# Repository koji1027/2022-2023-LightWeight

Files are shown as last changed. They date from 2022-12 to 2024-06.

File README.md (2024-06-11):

# 高崎高校物理部2年 2022-2023 LightWeight
高崎高校物理部2年チームのGithubリポジトリです。このリポジトリ上の全てのデータは，MIT-Lisenceに従ったうえでの仕様をすべて認めます．

各種リンク
* [ツイッター](https://twitter.com/takataka_robo)
* [ブログ](https://robocup-zunda.hatenablog.com)

## ロボットの機体の概要
ロボットの3Dデータです。-> https://a360.co/3iR0CL1  
3Dデータのリンクが切れている場合は，Hardware/robot.f3z をダウンロードしてFusion360からご覧ください．

以下に、今年度のロボットの基本的なスペックについて示します。
* Main  
  * Raspberry Pi PICO 1個
  * MPU-6050 1個
  * SSD1306 OLEDディスプレイ 1個

* IR Unit
  * TSSP58038 16個
  * TI CD74HC4067 SOIC 1個
  * XIAO SAMD21 1個

* Actuator
  * Maxon RE16 4個
  * Maxon GP16 1:19 4個
  * Pololu G2 18v17 4個
  * 自作オムニホイール 4個
  * XIAO RP2040 1個

* Line Unit
  * NJL7502L 32個
  * WS2812B 32個
  * TI CD74HC4067 SOIC 2個

* Cam
  * OpenMV H7 R2 もしくは UnitV 1個
  
## コーディング規則
簡単なコーディング規則を定めておきます。  
### ファイル構成
プログラムの中核部分を `main.cpp`に書くようにしてください。初見でプログラムを見た際にこのプログラムで大方何をやっているかわかるようにすることを意識してください。`setup()`と`loop()`は他のファイルへ移すことは禁止します。特定の機能にたくさんの記述が必要な場合にはライブラリにしてインクルードしてください。その際、インクルードガードをなるべくつけるようにしましょう。

### 変数・関数・クラス
それぞれの名前は、追加情報なしでもおおよそ役割が推測できる名前にしてくだいさい。例えば、`flag`などといいう名前では、なんのフラグなのかわからないので、`line_flag`などわかりやすい配慮をしてください。定数は、原則大文字で命名してください。  
各ユニットごとに、クラスを作成するようにして下さい。特定のユニットに依存した変数や関数はグローバルで作成するのではなく、各クラスのメンバ変数・関数にしましょう。メンバ変数・関数はできる限り`private`に閉じ込めることが望ましいです。

##コンタクト
もし、なにかありましたらチームリーダへ連絡していただけると幸いです。  
Mail📧&emsp;nkoji.personal@gmail.com&emsp;&emsp;[Twitter](https://twitter.com/negi_robo)

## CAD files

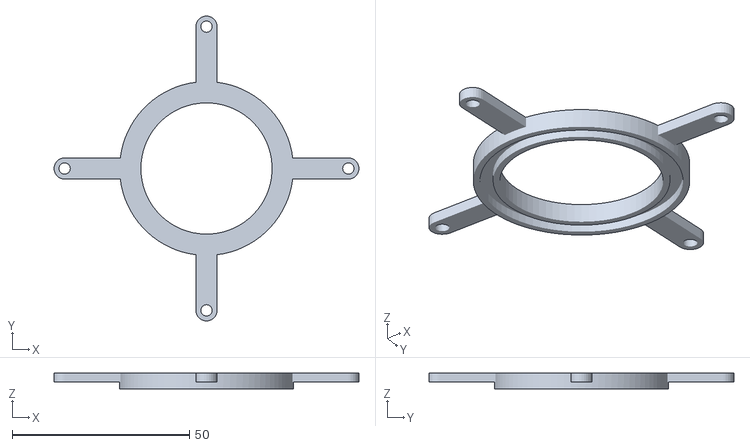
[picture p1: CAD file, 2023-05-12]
Hardware/STL/Pipe Mount GK.stl
86.0 x 86.0 x 4.50

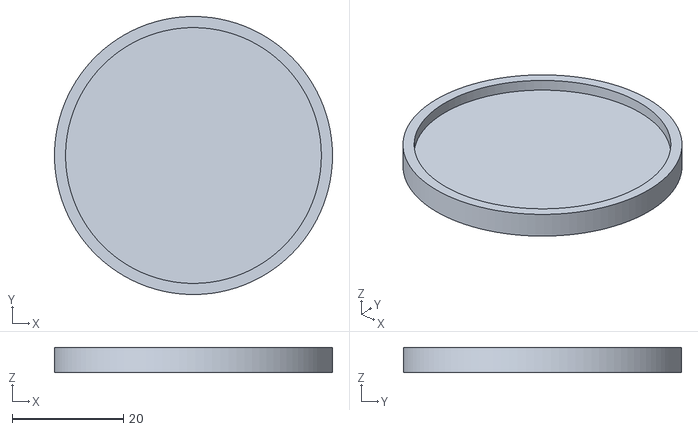
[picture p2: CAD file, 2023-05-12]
Hardware/STL/Top Marker GK.stl
50.0 x 50.0 x 4.50

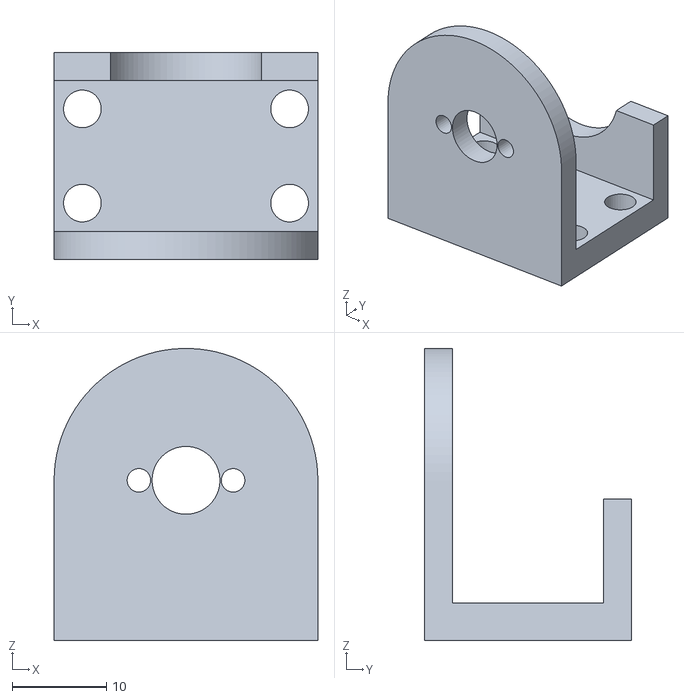
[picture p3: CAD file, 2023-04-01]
Hardware/STL/Motor Mount.stl
28.0 x 22.0 x 31.0

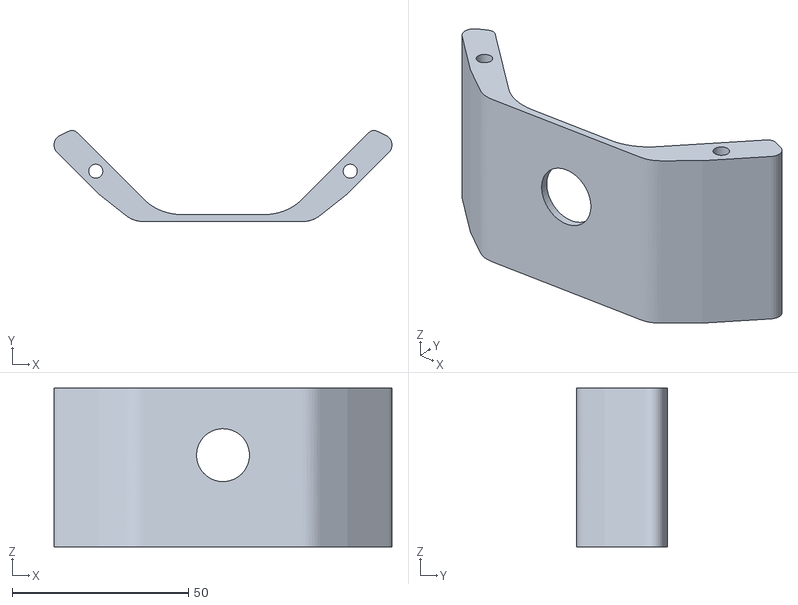
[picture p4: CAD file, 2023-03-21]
Hardware/STL/Front.stl
95.8 x 25.8 x 45.0

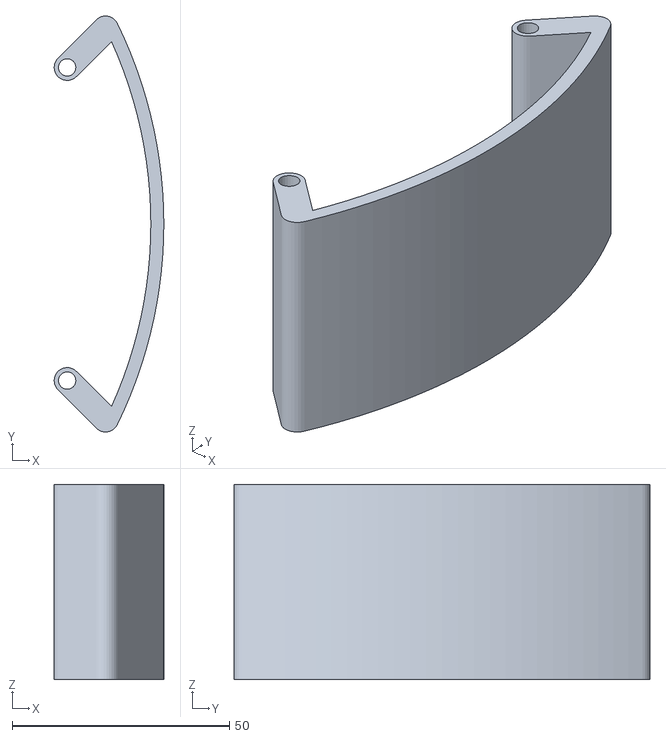
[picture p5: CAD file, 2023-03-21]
Hardware/STL/Right Cover.stl
25.3 x 95.8 x 45.0

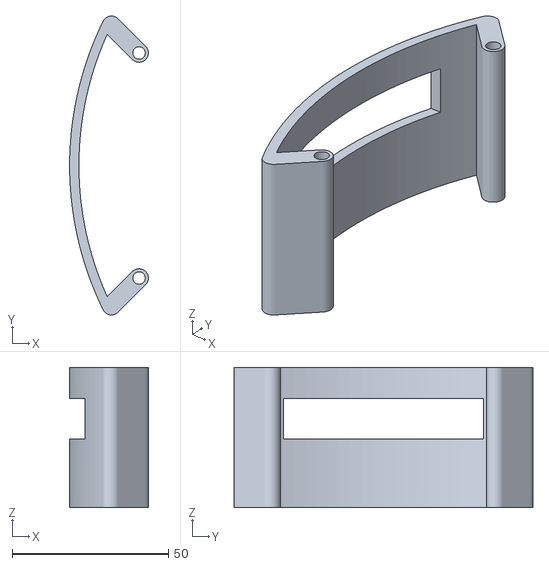
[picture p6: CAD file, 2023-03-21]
Hardware/STL/Left Cover.stl
25.3 x 95.8 x 45.0

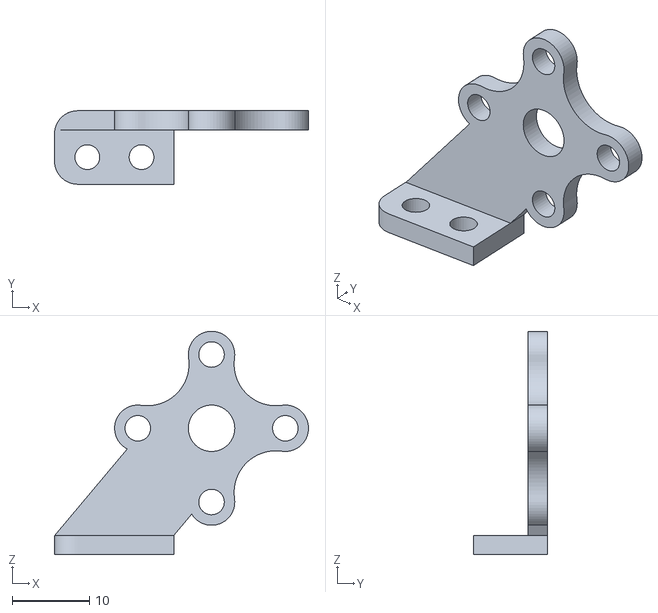
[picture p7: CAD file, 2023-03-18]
Hardware/STL/dribbler.stl
32.8 x 9.50 x 28.8

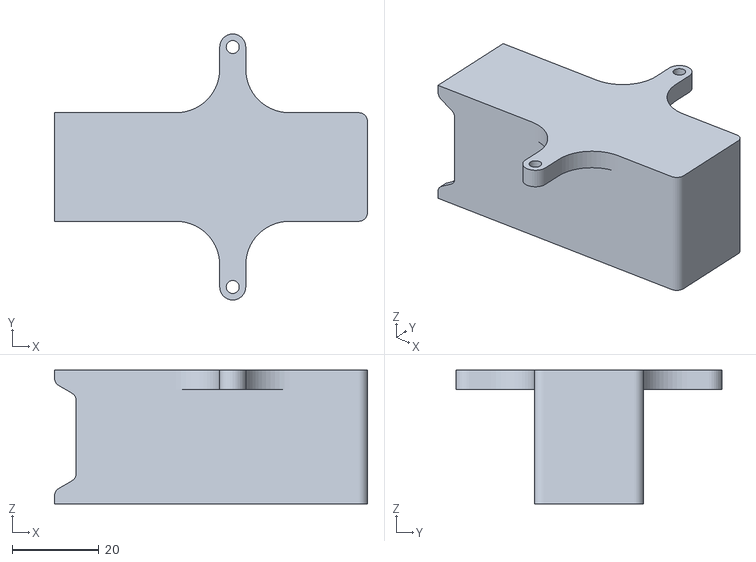
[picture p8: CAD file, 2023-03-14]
Hardware/STL/Battery Case.stl
72.0 x 61.2 x 30.8

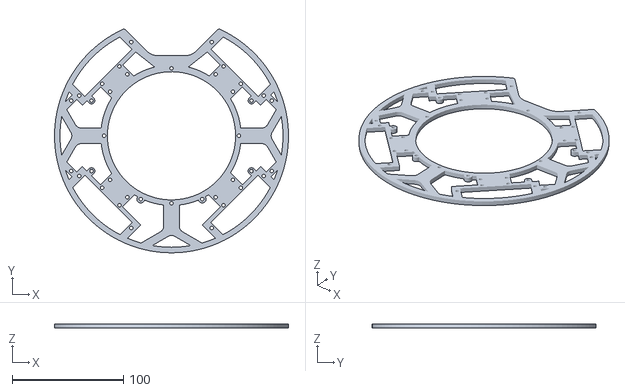
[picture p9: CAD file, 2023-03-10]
Hardware/STL/Bottom.stl
210.0 x 200.7 x 4.00

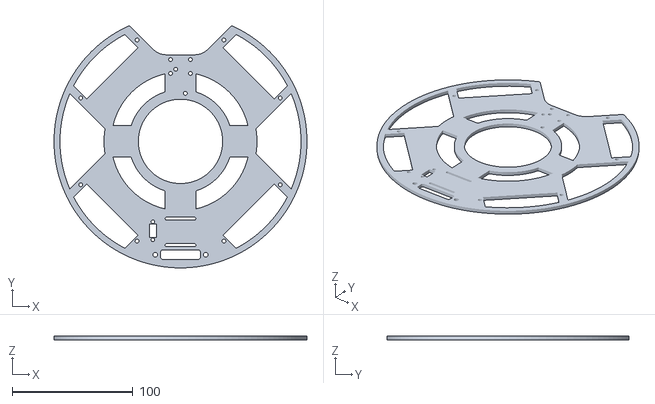
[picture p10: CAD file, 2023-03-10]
Hardware/STL/Top.stl
210.0 x 200.7 x 3.00

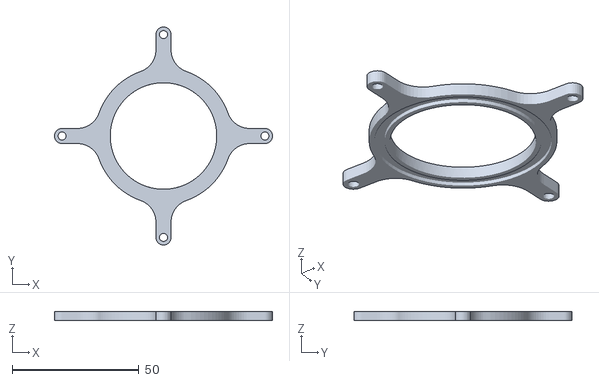
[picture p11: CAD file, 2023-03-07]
Hardware/STL/Pipe Mount FW.stl
86.0 x 86.0 x 3.50

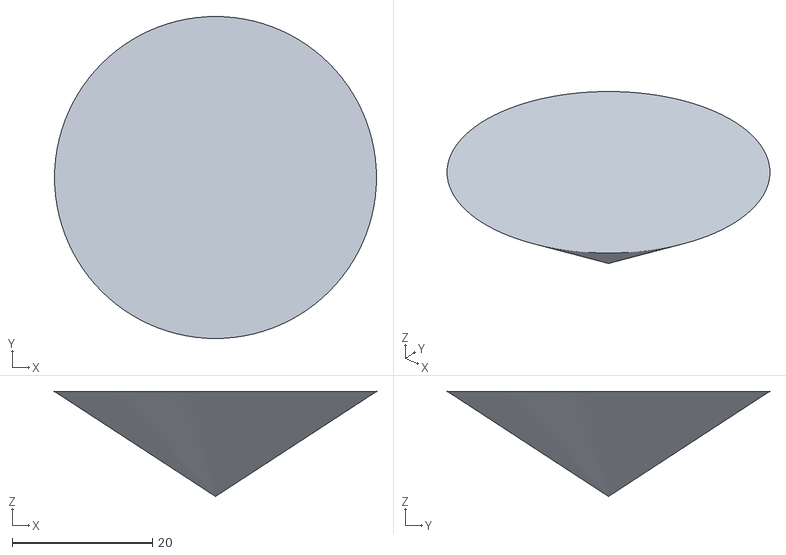
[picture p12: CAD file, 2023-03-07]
Hardware/STL/Mirror 円錐.stl
46.0 x 46.0 x 15.0

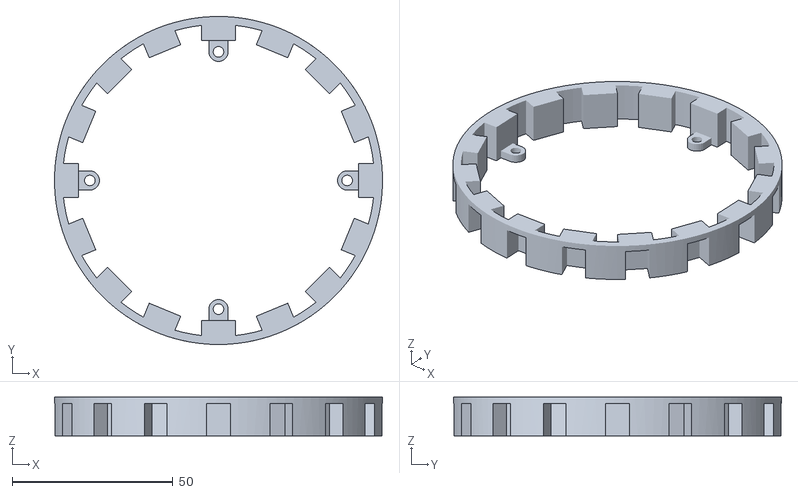
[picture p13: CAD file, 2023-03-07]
Hardware/STL/IR Cover.stl
102.0 x 102.0 x 12.0

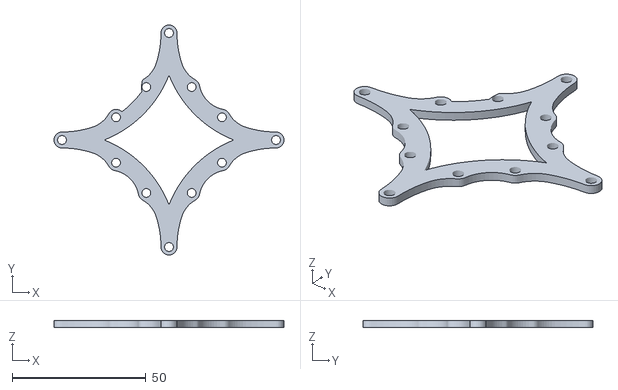
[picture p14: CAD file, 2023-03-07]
Hardware/STL/UnitV mount.stl
86.0 x 86.0 x 2.50

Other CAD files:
Hardware/STL/Back Cover.stl
Hardware/STL/Top Marker FW.stl
Hardware/STL/Test Omni Top.stl
Hardware/STL/OpenMV Mount.stl
Hardware/PCB/Controller.f3z
Hardware/PCB/MotorDriverMount(DRV8874).f3z
Hardware/PCB/MotorDriverMount(Pololu G2).f3z
Hardware/PCB/PowerSupplyBoard.f3z
Hardware/STL/Camera.stl
Hardware/STL/Handle.stl
Hardware/STL/Omini_Bottom.stl
Hardware/STL/Omini_Top.stl
Hardware/STL/OmniWheel_Rev2_1.stl
Hardware/STL/OmniWheel_Rev2_2.stl
Hardware/STL/Test Omni Bottom.stl

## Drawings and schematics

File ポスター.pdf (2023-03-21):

# 高崎高校物理部 二年 Member

## スムーズなチーム連携

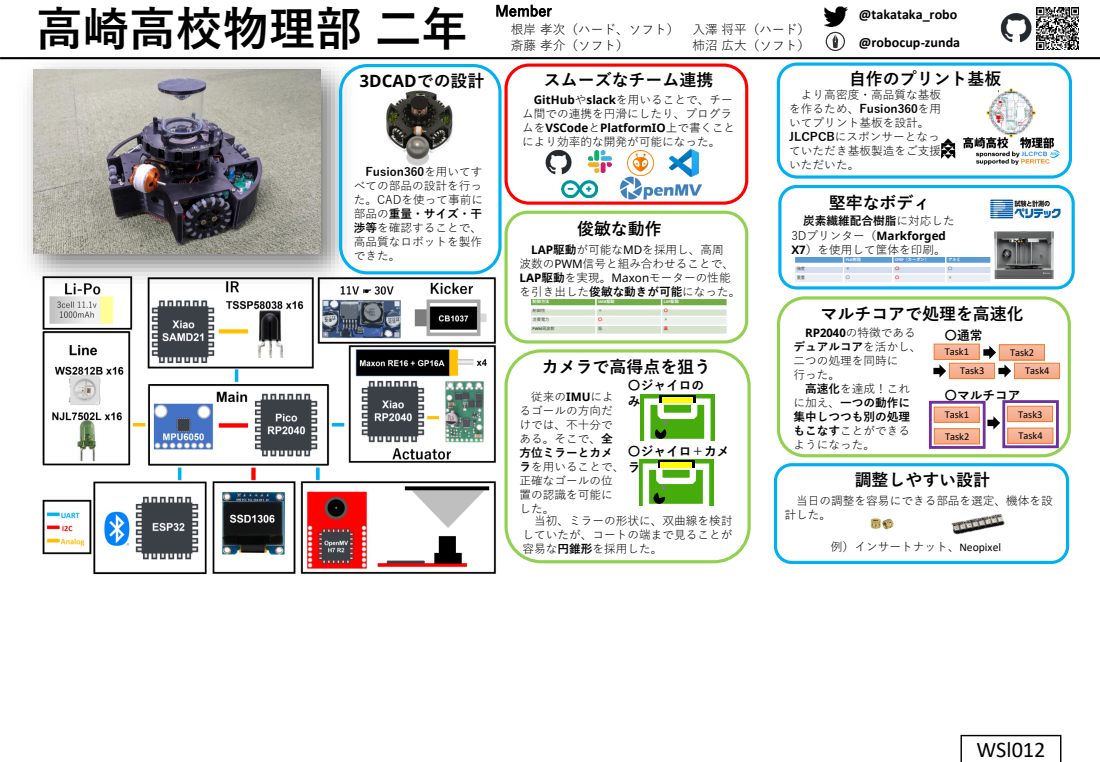
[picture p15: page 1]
斎藤 孝介（ソフト）; 柿沼 広大（ソフト）; @takataka_robo; @robocup-zunda; LAP駆動が可能なMDを採用し、高周 波数のPWM信号と組み合わせることで、 LAP駆動を実現。Maxonモーターの性能 を引き出した俊敏な動きが可能になった。; 俊敏な動作; GitHubやslackを用いることで、チー ム間での連携を円滑にしたり、プログラ ムをVSCodeとPlatformIO上で書くこと により効率的な開発が可能になった。; 堅牢なボディ; 炭素繊維配合樹脂に対応した 3Dプリンター（Markforged X7）を使用して筐体を印刷。; カメラで高得点を狙う; 従来のIMUによ るゴールの方向だ けでは、不十分で ある。そこで、全 方位ミラーとカメ ラを用いることで、 正確なゴールの位 置の認識を可能に した。 当初、ミラーの形状に、双曲線を検討 していたが、コートの端まで見ることが 容易な円錐形を採用した。; 〇ジャイロの み; 〇ジャイロ＋カメ ラ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

根岸 孝次（ハード、ソフト） 入澤 将平（ハード）

PLA樹脂 | CFRP（カーボン） | アルミ

制御方法 | SMB駆動 | LAP駆動

制御性 | × | 〇

消費電力 | 〇 | ×

PWM周波数 | 低 | 高

# 高崎高校物理部 二年 Member

## 堅牢なボディ

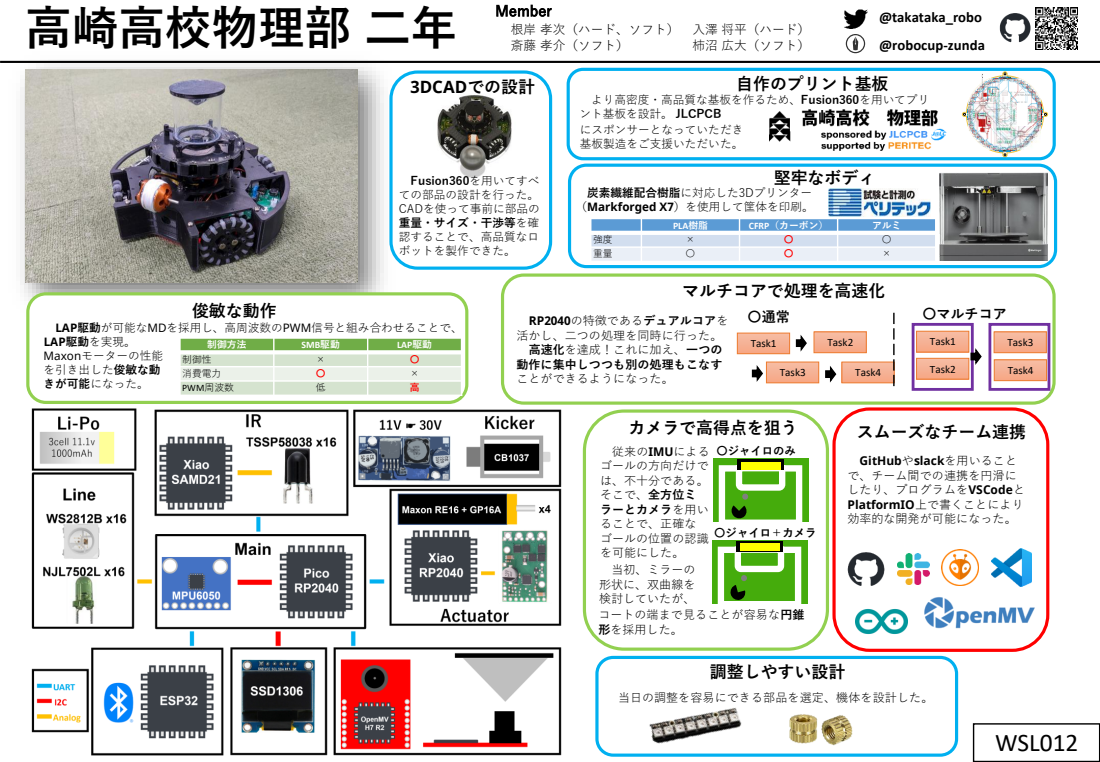
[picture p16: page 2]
斎藤 孝介（ソフト）; 柿沼 広大（ソフト）; @takataka_robo; @robocup-zunda; LAP駆動が可能なMDを採用し、高周波数のPWM信号と組み合わせることで、 LAP駆動を実現。; 俊敏な動作; スムーズなチーム連携; GitHubやslackを用いること で、チーム間での連携を円滑に したり、プログラムをVSCodeと PlatformIO上で書くことにより 効率的な開発が可能になった。; 炭素繊維配合樹脂に対応した3Dプリンター （Markforged X7）を使用して筐体を印刷。; カメラで高得点を狙う; 従来のIMUによる ゴールの方向だけで は、不十分である。 そこで、全方位ミ ラーとカメラを用い ることで、正確な ゴールの位置の認識 を可能にした。 当初、ミラーの 形状に、双曲線を 検討していたが、; 〇ジャイロのみ; 〇ジャイロ＋カメラ; マルチコアで処理を高速化; RP2040の特徴であるデュアルコアを 活かし、二つの処理を同時に行った。 高速化を達成！これに加え、一つの 動作に集中しつつも別の処理もこなす ことができるようになった。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

根岸 孝次（ハード、ソフト） 入澤 将平（ハード）

PLA樹脂 | CFRP（カーボン） | アルミ

強度 | × | 〇 | 〇
重量 | 〇 | 〇 | ×

制御方法 | SMB駆動 | LAP駆動
制御性 | × | 〇
消費電力 | 〇 | ×
PWM周波数 | 低 | 高

# Xiao

# TSSP580

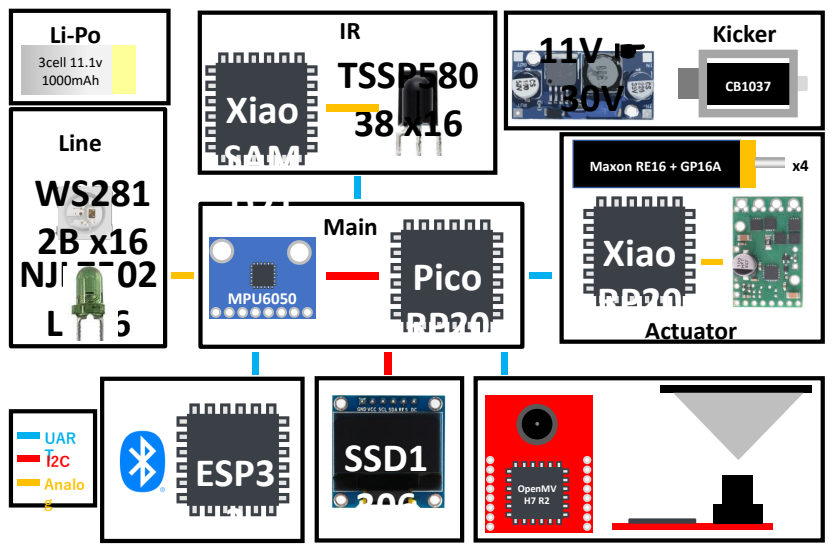
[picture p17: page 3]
Pico RP20 40; MPU6050; Main; NJL7502 L x16; Line; SAM D21; Actuator; 3cell 11.1v 1000mAh; Kicker; Xiao RP20 40; Maxon RE16 + GP16A; ESP3 2; OpenMV H7 R2; SSD1 306; UAR TI2C; Analo g

# Smooth

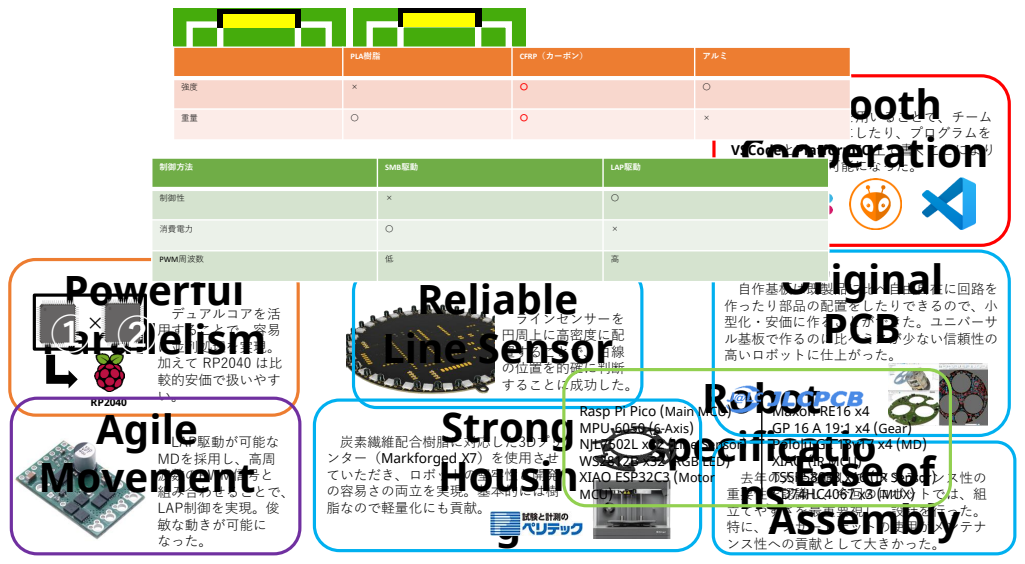
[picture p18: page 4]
Robot specificatio ns; Powerful Parallelism; デュアルコアを活 用することで、容易 に並列処理を実現。 加えて RP2040 は比 較的安価で扱いやす い。; Reliable Line Sensor; ラインセンサーを 円周上に高密度に配 置することで、白線 の位置を的確に判断 することに成功した。; LAP駆動が可能な MDを採用し、高周 波数のPWM信号と 組み合わせることで、 LAP制御を実現。俊 敏な動きが可能に なった。; Agile Movement; Strong Housin g; Cooperation; GitHubやslackを用いることで、チーム 間での連携を円滑にしたり、プログラムを VSCodeとPlatformIO上で書くことにより 効率的な開発が可能になった。; Ease of Assembly; 去年の大会を通して、メンテナンス性の 重要性を認識し、今回のロボットでは、組 立てやすさを最重要視し、設計を行った。 特に、インサートナットの使用がメンテナ ンス性への貢献として大きかった。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

PLA樹脂 | CFRP（カーボン） | アルミ

制御方法 | SMB駆動 | LAP駆動

制御性 | × | 〇

消費電力 | 〇 | ×

PWM周波数 | 低 | 高

Rasp Pi Pico (Main MCU)
MPU-6050 (6-Axis)
NJL7502L x32 (Line Sensor)
WS2812B x32 (RGB LED)
XIAO ESP32C3 (Motor
MCU)

炭素繊維配合樹脂に対応した3Dプリ
ンター（Markforged X7）を使用させ
ていただき、ロボットの堅牢性と開発
の容易さの両立を実現。基本的には樹
脂なので軽量化にも貢献。

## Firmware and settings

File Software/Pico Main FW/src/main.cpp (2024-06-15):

// Arduinoライブラリのインクルード
#include <Arduino.h>

// ライブラリのインクルード
#include <Adafruit_NeoPixel.h>
#include <Adafruit_SSD1306.h>
#include <Servo.h>
#include <stdlib.h>

// 自作ライブラリのインクルード
#include "MPU6050/gyro.h"
#include "line.h"

// 定数の宣言
#define SERIAL_BAUD 115200  // デバッグ用のシリアル通信のボーレート
#define MOTOR_BAUD 115200   // モーターの制御マイコンとの通信のボーレート
#define IR_BAUD 115200      // 赤外線センサー制御マイコンとの通信のボーレート
#define ESP32_BAUD 115200   // ESP32(Bluetooth通信)との通信のボーレート
#define OPENMV_BAUD 115200  // OpenMVとの通信のボーレート
#define OpenMV Serial1      // OpenMVとの通信のシリアルポート
// よく使う角度を定数に保存しておく
#define PI_THIRDS PI / 3.0
#define TWO_THIRDS_PI PI * 2.0 / 3.0
#define PI_EIGHTHS PI / 8.0
#define THREE_EIGHTHS_PI PI * 3.0 / 8.0
#define FIVE_EIGHTHS_PI PI * 5.0 / 8.0
// 回り込みのための計算式の係数
#define CIRC_BASE pow(0.6, 1.0 / 20.0)
#define CIRC_WEIGHT 3.5
// 機体の速度
#define CIRC_SPEED 160
#define STRAIGHT_SPEED 150
#define ESC_LINE_SPEED 190
// ゴールの角度について
#define GOAL_WEIGHT 1.4  // OpenMVからのゴールの角度を使用する際の重み
#define MAX_SIGNAL 2200  // OpenMVからの信号の最大値
#define MIN_SIGNAL 1000  // OpenMVからの信号の最小値
// ピン番号の定義
#define ESC_PIN D14  // ESC(ブラシレスモータードライバー)の制御ピン番号
#define LED_PIN D15  // LEDのピン番号
#define LED_NUM 32   // ラインセンサのLEDの数
// 操作モニターの設定
#define SCREEN_WIDTH 128     // 画面の幅
#define SCREEN_HEIGHT 64     // 画面の高さ
#define SCREEN_ADDRESS 0x3C  // SD1306のアドレス

const uint8_t button_pin[3] = {D18, D19, D20};  // 操作ボタンのピン番号

// インスタンスの生成
Gyro gyro;
Line line;
// Raspberry Pi pico では，PIOという内臓のコンピュータを利用することで，ハードウェアシリアルに似たソフトウェアシリアルを実装されている．
// ハードウェアシリアルが足りのないので，ソフトウェアシリアルを利用する．
SerialPIO motor(D17, D16, 32);  // SerialPIO name(TX, RX, buffer size) の形で宣言する．
SerialPIO ir(D0, D1, 32);
// SerialPIO esp32(D22, D21, 32); //これを使うとプログラムがバグる（詳細は忘れた）．多分，SerialPIOを使いすぎている．
Servo esc;
Adafruit_SSD1306 display(SCREEN_WIDTH, SCREEN_HEIGHT, &Wire, -1);  // モニター

// 全体の制御に関する変数
bool game_flag = false;            // ゲーム中かどうかのフラグ　0:ゲーム中でない, 1:ゲーム中
bool line_set_threshold_flag = 0;  // ラインセンサーの閾値設定フラグ（何に使っていたか忘れた）
double battery_voltage = 0;        // バッテリーの電圧(使ってない)
bool battery_flag = 0;             // バッテリーの電圧が低電圧かどうかのフラグ(使ってない)

// モーターの制御系
// ロボットから見た相対的な角度
double move_angle = 0;     // 進行方向（-PI ~ PI）
double goal_angle = 0;     // ゴールの角度（-PI ~ PI）
uint16_t goal_size = 0;    // ゴールのサイズ(なんで実装したか忘れた)
double machine_angle = 0;  // ロボットに向かせる角度（-PI ~ PI）

// コート全体を俯瞰した時の絶対的な角度
// ゲーム開始時の正面（敵ゴール）方向を０°とし、右回転が正、左回転が負とする。
double abs_move_angle = 0;  // 進行方向（-PI ~ PI）（絶対角度）
double abs_goal_angle = 0;  // ゴールの角度（-PI ~ PI）（絶対角度）
double abs_line_angle = 0;  // ラインの角度（-PI ~ PI）（絶対角度）

bool goal_flag = 0;           // 0:ゴールなし, 1:ゴールあり
uint8_t goal_flag_ratio = 0;  // 忘れた(斎藤に聞けばわかるかも)
uint8_t goal_flag_count = 0;  // 忘れた(斎藤に聞けばわかるかも)
uint8_t speed = 0;            // 速度（0~254）
uint8_t motor_flag = 0;       // モーターの状態についてのフラグ 0: normal, 1: release, 2 or others: brake（0~254）

unsigned long long display_refresh_time = 0;  // ディスプレイのリフレッシュ時間

// fpsを算出するための変数
unsigned long long start_time = 0;
unsigned long long end_time = 0;
int fps = 0;

// 赤外線センサー制御系
double ir_angle = 0;      // 赤外線センサーの角度（-PI ~ PI）
double abs_ir_angle = 0;  // 赤外線センサーの角度（-PI ~ PI）（絶対角度）
uint8_t ir_dist = 0;      // 赤外線センサーの距離（0~254[cm]）(使い物にならなかった)
uint8_t ir_flag = 0;      // ボールが検知されたかどうかのフラグ 0: 有り, 1: なし (0~254)

// 関数の宣言 (setup, loop以外は宣言はここで行い、定義は後で行う)
void motor_uart_send(void);                    // モーター制御系の送信関数
void ir_uart_recv(void);                       // 赤外線センサー制御系の受信関数
void openmv_uart_recv(void);                   // OpenMVとの通信の受信関数
void push_button(uint gpio, uint32_t events);  // ボタンの処理
void line_set_threshold(void);                 // 閾値の自動設定
void bldc_init(void);                          // ブラシレスモータードライバーの初期化
void bldc_drive(uint16_t volume);              // ブラシレスモータードライバーの制御
double normalize_angle(double angle);          // 角度を-πからπまでに調整
void esc_line(void);                           // ライン退避
void refresh_display(void);                    // ディスプレイのリフレッシュ

void setup(void) {
    // put your setup code here, to run once:
    // 各シリアル通信の開始
    Serial.begin(SERIAL_BAUD);
    OpenMV.setTX(D12);  // OpenMVとの通信のピン番号の設定
    OpenMV.setRX(D13);  // OpenMVとの通信のピン番号の設定
    OpenMV.begin(OPENMV_BAUD);
    motor.begin(MOTOR_BAUD);
    while (!motor);  // モーター制御マイコンとの通信の確立
    ir.begin(IR_BAUD);
    while (!ir);  // 赤外線センサー制御マイコンとの通信の確立
    // 6軸センサとラインセンサの初期化
    gyro.begin();
    line.begin();
    // bldc_init();　// ブラシレスモータードライバーの初期化(ドリブラー非搭載となったので不要)
    // bldc_drive(0);

    // ボタンの初期化
    pinMode(button_pin[0], INPUT_PULLUP);
    pinMode(button_pin[1], INPUT_PULLUP);
    pinMode(button_pin[2], INPUT_PULLUP);

    analogReadResolution(10);  // アナログリードの解像度を10bitに設定

    // NeoPixelの初期化(ラインセンサのLED)
    // 使い方はググってくれ
    Adafruit_NeoPixel *led = NULL;
    led = new Adafruit_NeoPixel(LED_NUM, LED_PIN, NEO_GRB + NEO_KHZ800);
    for (int i = 0; i < LED_NUM; i++) {
        led->setPixelColor(i, led->Color(255, 0, 0));
    }
    led->setBrightness(200);  // LEDの明るさを設定(0~255)
    led->show();

    delete (led);  // メモリの解放(多分いらない．昔Neopixelが原因でコードが停止するバグがあったときに一応入れた．)
}

// RP2040(マイコン)のコア0のsetupとloop
void loop(void) {
    if (line_set_threshold_flag) {  // 必要があればラインセンサーの閾値設定を行う
        line_set_threshold();
    }
    while (game_flag) {                                         // このwhile文の中でゲームが行われる
        start_time = micros();                                  // fpsの計算のための時間計測
        motor_flag = 0;                                         // モーターの状態を初期化
        battery_voltage = analogRead(A2) * 3.3 / 1023.0 * 4.0;  // バッテリーの電圧を計測(役に立たない．使ってない)
        gyro.getEuler();                                        // 6軸センサの角度(オイラー角）を取得．（オイラー角は角度の表現方法の一つ．自分で調べな．）
        if (millis() - display_refresh_time > 100) {            // ディスプレイのリフレッシュ（100msごとに行う）．while文の中で毎回行うとディスプレイとの通信に時間がかかってボトルネックになってしまう．
            refresh_display();
        }
        ir_uart_recv();      // 赤外線センサー制御系の受信
        openmv_uart_recv();  // OpenMVとの通信の受信
        line.read();         // ラインセンサーの読み取り
        // line.debug(); // ラインセンサーのデバッグ

        if (line.on_line) {                                 // ライン上にいる場合
            abs_line_angle = line.line_theta + gyro.angle;  // ラインの角度(絶対角度)を取得
            // ラインの角度が-π ~ πになるように調整
            if (abs_line_angle > PI) {
                abs_line_angle -= TWO_PI;
            } else if (abs_line_angle <= -PI) {
                abs_line_angle += TWO_PI;
            }
        }
        // 赤外線センサーの角度（絶対角度）を取得
        abs_ir_angle = ir_angle + gyro.angle;
        // 赤外線センサーの角度が-π ~ πになるように調整
        abs_ir_angle = fmod(abs_ir_angle, TWO_PI);
        if (abs_ir_angle > PI) {
            abs_ir_angle -= TWO_PI;
        }
        if (abs_ir_angle < -PI) {
            abs_ir_angle += TWO_PI;
        }
        if (line.on_line) {  // ライン上にいる場合
            // ラインの角度による分類を以下に示す
            // 前： -PI/8 ~ PI/8, 右前: PI/8 ~ 3PI/8, 右: 3PI/8 ~ 5PI/8, 右後ろ: 5PI/8 ~ 7PI/8,
            // 後ろ: 7PI/8 ~ -7PI/8, 左後ろ: -7PI/8 ~ -5PI/8, 左: -5PI/8 ~ -3PI/8, 左前: -3PI/8 ~ -PI/8
            // ライン退避がめっちゃぐちゃぐちゃになっていしまったのは申し訳ない．大会当日はコードを綺麗に整える余裕がなかった．（やってみればわかる．）
            if (abs_line_angle > PI * 3.0 / 8.0 && abs_line_angle <= PI * 5.0 / 8.0)  // ラインが右にある
            {
                if (line.line_state_flag == 0 || line.line_state_flag == 2) {
                    line.line_state_flag = 2;
                    if (abs_ir_angle <= PI / 2.0 && abs_ir_angle >= 0) {
                        abs_move_angle = -PI / 9.0;
                        move_angle = abs_move_angle - gyro.angle;
                        speed = 100;
                        motor_flag = 0;
                        // Serial.println("front");
                    } else if (abs_ir_angle >= PI / 2.0 || abs_ir_angle <= -PI / 3.0) {
                        abs_move_angle = -PI * 8.0 / 9.0;
                        move_angle = abs_move_angle - gyro.angle;
                        speed = 100;
                        motor_flag = 0;
                        // Serial.println("back");
                    } else if (abs_ir_angle < 0 && abs_ir_angle >= -PI / 3.0) {
                        line.on_line = false;
                        // Serial.println("front");
                    }
                } else {
                    esc_line();
                }
            } else if (abs_line_angle <= -PI * 3.0 / 8.0 && abs_line_angle > -PI * 5.0 / 8.0)  // ラインが左にある
            {
                // Serial.println("left");
                if (line.line_state_flag == 0 || line.line_state_flag == 4) {
                    line.line_state_flag = 4;
                    if (abs_ir_angle >= -PI / 2.0 && abs_ir_angle <= 0) {
                        abs_move_angle = PI / 9.0;
                        move_angle = abs_move_angle - gyro.angle;
                        speed = 100;
                        motor_flag = 0;
                        // Serial.println("front");
                    } else if (abs_ir_angle <= -PI / 2.0 || abs_ir_angle >= PI / 3.0) {
                        abs_move_angle = PI * 8.0 / 9.0;
                        move_angle = abs_move_angle - gyro.angle;
                        speed = 100;
                        motor_flag = 0;
                        // Serial.println("back");
                    } else if (abs_ir_angle > 0 && abs_ir_angle <= PI / 3.0) {
                        line.on_line = false;
                        // Serial.println("front");
                    }
                } else {
                    esc_line();
                }
            } else if (abs_line_angle <= PI / 8.0 && abs_line_angle > -PI / 8.0)  // ラインが前にある
            {
                // Serial.println("front");
                if (line.line_state_flag == 0 || line.line_state_flag == 1) {
                    line.line_state_flag = 1;
                    esc_line();
                } else {
                    esc_line();
                }
            } else if (abs_line_angle <= PI * 3.0 / 8.0 && abs_line_angle > PI / 8.0)  // ラインが右前にある
            {
                // Serial.println("right front");
                if (line.line_state_flag == 0 || line.line_state_flag == 5) {
                    line.line_state_flag = 5;
                    esc_line();
                } else {
                    esc_line();
                }
            } else if (abs_line_angle <= -PI / 8.0 && abs_line_angle > -PI * 3.0 / 8.0)  // ラインが左前にある
            {
                // Serial.println("left front");
                if (line.line_state_flag == 0 || line.line_state_flag == 7) {
                    line.line_state_flag = 7;
                    esc_line();
                } else {
                    esc_line();
                }
            } else if (abs_line_angle <= PI * 7.0 / 8.0 && abs_line_angle > PI * 5.0 / 8.0)  // ラインが右後ろにある
            {
                // Serial.println("right back");
                if (line.line_state_flag == 0 || line.line_state_flag == 6) {
                    line.line_state_flag = 6;
                    esc_line();
                } else {
                    esc_line();
                }
            } else if (abs_line_angle <= -PI * 5.0 / 8.0 && abs_line_angle > -PI * 7.0 / 8.0)  // ラインが左後にある
            {
                // Serial.println("left back");
                if (line.line_state_flag == 0 || line.line_state_flag == 8) {
                    line.line_state_flag = 8;
                    esc_line();
                } else {
                    esc_line();
                }
            } else  // ラインが後ろにある
            {
                // Serial.println("back");
                if (line.line_state_flag == 0 || line.line_state_flag == 3) {
                    line.line_state_flag = 3;
                    if (abs_ir_angle <= -PI * 7.0 / 9.0 || abs_ir_angle > PI * 7.0 / 9.0) {
                        speed = 0;
                        motor_flag = 1;
                    } else if (abs_ir_angle > -PI * 7.0 / 9.0 && abs_ir_angle <= -PI / 2.0) {
                        speed = 0;
                        motor_flag = 1;
                    } else if (abs_ir_angle > -PI / 2.0 && abs_ir_angle < PI / 2.0) {
                        abs_move_angle = constrain(ir_angle, -PI / 4.0, PI / 4.0);
                        move_angle = abs_move_angle - gyro.angle;
                        speed = 100;
                        motor_flag = 0;
                    } else if (abs_ir_angle >= PI / 2.0 && abs_ir_angle <= PI * 7.0 / 9.0) {
                        speed = 0;
                        motor_flag = 1;
                    }
                } else {
                    esc_line();
                }
            }
        }
        if (!line.on_line) {           // ライン上にいない場合
            line.line_state_flag = 0;  // ラインの状態を初期化
            if (goal_flag) {           // ゴールがある場合．ゴールの角度に基づいて機体が向くべき角度を調整する．
                // この辺の処理はよくわからん（by根岸）．斎藤に聞いてくれ．
                if (goal_flag_ratio < 100) {
                    if (abs_goal_angle > 0) {
                        if (goal_flag_ratio <= 92) {
                            goal_flag_ratio += 8;
                        } else {
                            goal_flag_ratio = 100;
                        }
                    }
                    if (abs_goal_angle < 0) {
                        if (goal_flag_ratio <= 84) {
                            goal_flag_ratio += 16;
                        } else {
                            goal_flag_ratio = 100;
                        }
                    }
                }
                machine_angle = abs_goal_angle * GOAL_WEIGHT;
                if (machine_angle > -PI / 6 && gyro.angle < PI / 6) {
                    machine_angle += 0.7;
                    machine_angle *= 0.3;
                } else if (machine_angle < 0) {
                    machine_angle *= 0.8;
                }
                if (machine_angle > PI_THIRDS) {
                    machine_angle = PI_THIRDS;
                } else if (machine_angle < -PI_THIRDS) {
                    machine_angle = -PI_THIRDS;
                }
                machine_angle = normalize_angle(machine_angle);
            } else {
                // machine_angle = machine_angle * 0.9;
                if (machine_angle > 0.001) {
                    machine_angle -= 0.001;
                } else if (machine_angle < -0.001) {
                    machine_angle += 0.001;
                }
            }

            if (ir_flag) {                                 // ボールが検知された場合
                float circ_exp = pow(CIRC_BASE, ir_dist);  // 回り込みのための計算式．これがどうして導かれたかは謎．誰ももう覚えてない．
                // 計算で得られた角度が不適切な場合があるので，移動する方向を制限する．
                move_angle = ir_angle + constrain(ir_angle * circ_exp * CIRC_WEIGHT, -PI / 2.0, PI / 2.0);
                if (abs(move_angle) < PI / 6) {  // 移動する方向に応じて速度を変更する．
                    speed = STRAIGHT_SPEED;
                } else {
                    speed = CIRC_SPEED;
                }
            } else {  // ボールが検知されない場合．停止．
                move_angle = 0;
                speed = 0;
                motor_flag = 0;
            }
        }

        move_angle = normalize_angle(move_angle);  // 角度を-πからπまでに調整
        motor_uart_send();                         // モーター制御系の送信

        // ボタンの処理
        if (digitalRead(button_pin[0]) == LOW) {
            int cnt = 0;
            while (1) {
                if (digitalRead(button_pin[0]) == LOW) {
                    cnt++;
                    if (cnt == 100) {  // ボタンが十分な時間押されているかを確認（チャタリング対策）
                        break;
                    }
                } else {
                    cnt = 0;
                    break;
                }
                delay(2);
            }
            if (cnt == 100) {
                game_flag = 0;
                Serial.println("Game Stop");
            }
        }
        if (Serial.available()) {
            uint16_t volume = Serial.readStringUntil('\n').toInt();  // PCからのシリアル通信でモーターの速度を変更する（不要）.
            bldc_drive(volume);
        }
        end_time = micros();
        fps = 1000000.0 / (end_time - start_time);  // fpsの計算
    }
    if (digitalRead(button_pin[1]) == LOW) {
        int cnt = 0;
        while (1) {
            if (digitalRead(button_pin[1]) == LOW) {
                cnt++;
                if (cnt == 80) {  // ボタンが十分な時間押されているかを確認（チャタリング対策）
                    break;
                }
            } else {
                cnt = 0;
                break;
            }
            delay(2);
        }
        if (cnt == 80) {
            game_flag = 1;
            Serial.println("Game Start");
        }
    }

    // ゲームが始まっていない時
    move_angle = 0;
    speed = 0;
    motor_flag = 2;
    motor_uart_send();
}

// RP2024(マイコン)のコア1のsetupとloop
void setup1(void) {
}

void loop1(void) {
}

void motor_uart_send(void) {
    byte buf[8];
    buf[0] = constrain(motor_flag, 0, 254);    // 0: normal, 1: release, 2 or others: brake (0~254)
    uint16_t tmp = (move_angle + PI) * 100.0;  //-PI ~ PI -> 0 ~ 200PI
    buf[1] = tmp & 0b0000000001111111;         // 下位7bit
    buf[2] = tmp >> 7;                         // 上位2bit
    tmp = (gyro.angle + PI) * 100.0;           //-PI ~ PI -> 0 ~ 200PI
    buf[3] = tmp & 0b0000000001111111;         // 下位7bit
    buf[4] = tmp >> 7;                         // 上位3bit
    tmp = (machine_angle + PI) * 100.0;
    buf[5] = tmp & 0b0000000001111111;  // 下位7bit
    buf[6] = tmp >> 7;                  // 上位3bit
    buf[7] = constrain(speed, 0, 254);  // constrain(speed, 0, 254); // 0~254
    motor.write(255);                   // ヘッダー
    motor.write(buf, 8);
    motor.write(254);
    // Serial.println("Send");
}

void ir_uart_recv(void) {
    ir.write(255);  // ヘッダー
    unsigned long long request_time = micros();
    while (!ir.available()) {                   // データを受信するまで待つ
        if (micros() - request_time > 10000) {  // 10ms以上データが来ない場合は受信を諦める
            break;
        }
    }
    byte header = ir.read();  // ヘッダーを読み取る
    if (header != 255)
        return;  // ヘッダーが255でない場合は受信を諦める
    unsigned long long wait_time = micros();
    while (ir.available() < 4) {             // 4バイトのデータを受信するまで待つ
        if (micros() - wait_time > 10000) {  // 10ms以上データが来ない場合は受信を諦める
            while (ir.available()) {         // データが来ている場合は読み取る
                ir.read();
            }
            break;
        }
    }
    byte buf[4];  // データを格納するバッファ．データ構造については Xiao SAMD21 IRプロジェクトを参照
    ir.readBytes(buf, 4);
    if (buf[0] != 255 && buf[1] != 255 && buf[2] != 255 && buf[3] != 255) {
        ir_flag = buf[0];                                 // 0: normal, 1: stop (0~254)
        ir_angle = (buf[1] + buf[2] * 128) / 100.0 - PI;  // 0 ~ 200PI -> -PI ~ PI
        ir_dist = buf[3];                                 // 0~254[cm]
    }
}

void push_button(uint gpio, uint32_t events) {  // ボタンの処理（何してるか忘れた．解読する気もない．多分使ってない．）
    if (gpio == button_pin[0]) {
        gpio_set_irq_enabled(button_pin[0], GPIO_IRQ_EDGE_FALL, false);
        unsigned long long time1 = millis();
        while (digitalRead(button_pin[0]) == 0) {
            if (millis() - time1 > 1000) {
                break;
            }
        }
        // gyro.getEuler();
        // gyro.angle_offset = gyro.angle;
        game_flag = 1;
        // Serial.println("game start");
        gpio_set_irq_enabled(button_pin[0], GPIO_IRQ_EDGE_FALL, true);
    } else if (gpio == button_pin[1]) {
        gpio_set_irq_enabled(button_pin[1], GPIO_IRQ_EDGE_FALL, false);
        unsigned long long time1 = millis();
        while (digitalRead(button_pin[1]) == 0) {
            if (millis() - time1 > 1000) {
                break;
            }
        }
        if (!game_flag) {
            line_set_threshold_flag = 1;
        } else {
            gpio_set_irq_enabled(button_pin[1], GPIO_IRQ_EDGE_FALL, true);
        }
    } else if (gpio == button_pin[2]) {
        gpio_set_irq_enabled(button_pin[2], GPIO_IRQ_EDGE_FALL, false);
        unsigned long long time1 = millis();
        while (digitalRead(button_pin[2]) == 0) {
            if (millis() - time1 > 1000) {
                break;
            }
        }
        if (!line_set_threshold_flag) {
            game_flag = 0;
            // Serial.println("game stop");
            speed = 0;
            move_angle = 0;
            motor_flag = 1;
            motor_uart_send();
            display.clearDisplay();
            display.setCursor(0, 0);
            display.print("Waiting");
            display.display();
        }
        gpio_set_irq_enabled(button_pin[2], GPIO_IRQ_EDGE_FALL, true);
    }
}

void line_set_threshold() {  // ラインセンサーの閾値自動設定
    // 何しているかざっくりと解説．
    // ラインセンサーの閾値を自動設定する．
    // 一定時間の間，ロボットを白線と緑の部分を行ったり来たりさせる．その間，ラインセンサーの値を取得し，その平均値（多分）を閾値とする．
    Serial.println("Start auto threshold setting");
    Serial.println("Please push middle button to start");
    Serial.println("wait...");
    display.clearDisplay();
    display.setCursor(0, 0);
    display.setTextSize(1);
    display.setTextColor(WHITE);
    display.print("Auto Set Threshold");
    display.setCursor(0, 8);
    display.print("Please Push Mid-Button");
    display.display();
    uint8_t cnt = 0;
    delay(1000);
    while (1) {
        if (digitalRead(button_pin[1]) == HIGH) {
            cnt = 0;
            delay(10);
        } else {
            cnt++;
            delay(10);
        }
        if (cnt > 5) {
            break;
        }
    }
    display.clearDisplay();
    display.setCursor(0, 0);
    display.print("Start");
    display.setCursor(0, 8);
    display.print("Move the Robot");
    display.display();
    delay(1000);
    // Serial.println("run");
    line.set_threshold();
    delay(1000);
    display.clearDisplay();
    display.setCursor(0, 0);
    display.print("Ended");
    display.setCursor(0, 8);
    display.print(line.ave_threshold);
    display.display();
    // Serial.println("End auto threshold setting");
    line_set_threshold_flag = false;
    gpio_set_irq_enabled(button_pin[1], GPIO_IRQ_EDGE_FALL, true);
}
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

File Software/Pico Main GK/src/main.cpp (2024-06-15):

// 細かいコメントは省略することがあります．その場合は，Pico Main FWプロジェクトのmain.cppを参照してください．
//  Arduinoライブラリのインクルード
#include <Arduino.h>

// ライブラリのインクルード
#include <Adafruit_NeoPixel.h>
#include <Adafruit_SSD1306.h>

// 自作ライブラリのインクルード
#include "MPU6050/gyro.h"
#include "line.h"

// 定数の宣言
#define SERIAL_BAUD 115200  // デバッグ用のシリアル通信のボーレート
#define MOTOR_BAUD 115200   // モーターの制御マイコンとの通信のボーレート
#define IR_BAUD 115200      // 赤外線センサー制御マイコンとの通信のボーレート
#define ESP32_BAUD 115200   // ESP32(Bluetooth通信)との通信のボーレート
#define OPENMV_BAUD 115200  // OpenMVとの通信のボーレート
#define OpenMV Serial1      // OpenMVとの通信のシリアルポート
// 機体の速度
#define GUARD_SPEED 180
#define BACK_SPEED 180
#define STRAIGHT_SPEED 180
#define ESC_LINE_SPEED 200
#define ATTACK_SPEED 180
#define SLIDE_SPEED 150
// ゴールの角度について
#define GOAL_WEIGHT 1.5  // OpenMVからのゴールの角度を使用する際の重み
#define MAX_SIGNAL 2200  // OpenMVからの信号の最大値
#define MIN_SIGNAL 1000  // OpenMVからの信号の最小値
// ピン番号の定義
#define LED_PIN D15  // LEDのピン番号
#define LED_NUM 32   // ラインセンサのLEDの数
// 操作モニターの設定
#define SCREEN_WIDTH 128     // 画面の幅
#define SCREEN_HEIGHT 64     // 画面の高さ
#define SCREEN_ADDRESS 0x3C  // SD1306のアドレス
// よく使う角度を定数に保存しておく
#define PI_THIRDS PI / 3.0
#define TWO_THIRDS_PI PI * 2.0 / 3.0
#define PI_NINTH PI / 9.0
#define PI_FOURTH PI / 4.0
#define PI_THREE_FOURTH PI * 3.0 / 4.0
#define PI_SIXTH PI / 6.0
#define PI_165_180 PI * 165 / 180
#define EIGHT_NINTH_PI PI * 8.0 / 9.0

const uint8_t button_pin[3] = {D18, D19, D20};  // ボタンのピン番号

// インスタンスの生成
Gyro gyro;
Line line;
// SerialPIOについては，Pico Main FWプロジェクトのmain.cppを参照
SerialPIO motor(D17, D16, 32);  // TX, RX, buffer size
SerialPIO ir(D0, D1, 32);

// 全体の制御系
bool game_flag = false;            // ゲームの開始フラグ
bool line_set_threshold_flag = 0;  // ラインセンサーの閾値設定フラグ
double battery_voltage = 0;        // バッテリーの電圧(使ってない)
bool battery_flag = 0;             // バッテリーの電圧が低電圧かどうかのフラグ(使ってない)

// モーターの制御系
// ロボットから見た相対的な角度
double move_angle = 0;                                 // 進行方向（-PI ~ PI）
double goal_angle = 0;                                 // ゴールの角度（-PI ~ PI）
double goal_angle_LPF = 0;                             // ゴールのサイズ(なんで実装したか忘れた)
double pre_goal_angle[5] = {0.0, 0.0, 0.0, 0.0, 0.0};  // ゴールの角度の過去の値

// コート全体を俯瞰した時の絶対的な角度
// ゲーム開始時の正面（敵ゴール）方向を０°とし、右回転が正、左回転が負とする。
double abs_move_angle = 0;
double abs_goal_angle = 0;
double abs_goal_angle_LPF = 0;
double abs_goal_angle_inv = 0;
double abs_line_angle = 0;

// その他
double machine_angle = 0;  // ロボットに向かせる角度（-PI ~ PI）
bool goal_flag = 0;        // 0:ゴールなし, 1:ゴールあり
bool corner_flag = 0;      // GKゾーンのかどにいるかどうか
uint8_t goal_flag_ratio = 0;
uint8_t goal_flag_count = 0;
uint8_t goal_dist = 0;

uint8_t speed = 0;       // 速度（0~254）
uint8_t motor_flag = 0;  // 0: normal, 1: release, 2 or others: brake（0~254）

// 赤外線センサー制御系
double ir_angle = 0;  // 赤外線センサーの角度（-PI ~ PI）
double abs_ir_angle = 0;
uint8_t ir_dist = 0;  // 赤外線センサーの距離（0~254[cm]）
uint8_t ir_flag = 0;  // 0: normal, 1: stop (0~254)

// 関数の宣言 (setup, loop以外は宣言はここで行い、定義は後で行う)
void motor_uart_send(void);  // モーターの制御系の送信関数
void ir_uart_recv(void);     // 赤外線センサーの制御系の受信関数
void openmv_uart_recv(void);
void line_set_threshold(void);  // 閾値の設定
void bldc_init(void);
void bldc_drive(uint16_t volume);
double normalize_angle(double angle);  // 角度を-πからπまでに調整
void line_set_threshold();

void setup(void) {
    // put your setup code here, to run once:
    Serial.begin(SERIAL_BAUD);
    gyro.begin();
    motor.begin(MOTOR_BAUD);
    while (!motor);
    ir.begin(IR_BAUD);
    while (!ir);
    OpenMV.setTX(D12);
    OpenMV.setRX(D13);
    OpenMV.begin(OPENMV_BAUD);
    line.begin();
    pinMode(button_pin[0], INPUT_PULLUP);
    pinMode(button_pin[1], INPUT_PULLUP);
    pinMode(button_pin[2], INPUT_PULLUP);
    Adafruit_NeoPixel *led = NULL;
    led = new Adafruit_NeoPixel(LED_NUM, LED_PIN, NEO_GRB + NEO_KHZ800);
    for (int i = 0; i < LED_NUM; i++) {
        led->setPixelColor(i, led->Color(255, 0, 0));
    }
    led->setBrightness(255);
    led->show();

    delete (led);
}
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

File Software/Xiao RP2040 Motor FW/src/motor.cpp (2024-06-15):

#include "motor.h"

// モーターの初期化
void Motor::begin(void) {
    analogWriteResolution(PWM_RES);  // PWMの分解能を設定
    analogWriteFreq(PWM_FREQ);       // PWMの周波数を設定
    for (uint8_t i = 0; i < MOTOR_NUM; i++) 
    {
        pinMode(PWM_PIN[i], OUTPUT);
        digitalWrite(PWM_PIN[i], HIGH);  // LAP駆動なのでHIGHに固定
        pinMode(DIR_PIN[i], OUTPUT);
        analogWrite(DIR_PIN[i],MAX_PWM / 2);  // LAP駆動なのでDIRでPWM出力 (デューティ比50%)
    }
}

// モーターを制御
void Motor::drive(int *p) {
    uint16_t duty[MOTOR_NUM];  // デューティ比
    for (uint8_t i = 0; i < MOTOR_NUM; i++) {
        duty[i] = 256 + p[i];  // デューティ比を計算
        digitalWrite(PWM_PIN[i], HIGH);
        analogWrite(DIR_PIN[i], duty[i]);
    }
}

// モーターをブレーキ
void Motor::brake(void) {
    for (uint8_t i = 0; i < MOTOR_NUM; i++) {
        digitalWrite(PWM_PIN[i], LOW);  // LAP駆動では無い
        analogWrite(DIR_PIN[i], 0);
    }
}

// モーターを解放（現状では，ブレーキと同じ動作をする）
void Motor::release(void) {
    for (uint8_t i = 0; i < MOTOR_NUM; i++) {
        digitalWrite(PWM_PIN[i], LOW);
        analogWrite(DIR_PIN[i], 0);
    }
}

// 各モーターの出力を計算
void Motor::cal(double move_angle, double gyro_angle, double machine_angle,
                uint8_t speed) {
    double power_ratio[MOTOR_NUM];  // 各モーターの出力比
    double gyro_angle_diff =
        machine_angle -
        gyro_angle;                          // ジャイロの角度と機体の向いているべき方向の差
    unsigned long long now_time = micros();  // 現在の時間
    unsigned long long dt =
        now_time - pre_time;                    // 前回の処理を行った時の時間からの経過時間
    double p, i, d;                             // PID制御のP, I, D
    p = gyro_angle_diff * KP;                   // P制御
    i = gyro_angle_diff * dt * KI / 1000000.0;  // I制御
    d = gyro_angle_diff * 1000000.0 / dt * KD;  // D制御
    double pid = (p + i + d) / PI * 180.0;      // PID制御による出力の合計
    // ジャイロセンサーの角度と機体が向くべき角度との差が45°以下のとき，行きたい方向へ進むように出力を計算する．
    if (abs(gyro_angle_diff) < PI / 4.0) {
        // モーターの出力比を計算
        for (uint8_t i = 0; i < MOTOR_NUM; i++) {
            power_ratio[i] = sin(
                move_angle -
                MOTOR_RAD
                    [i]);  // モーターの出力比を計算（計算法については，別途説明）
        }
        double max = 0;  // 最大の出力比
        for (uint8_t i = 0; i < MOTOR_NUM; i++) {
            if (abs(power_ratio[i]) > max) {
                max = abs(power_ratio[i]);
            }
        }
        // 出力比が最大のモーターの出力がspeedになるように調整
        if (max > 0) {
            for (uint8_t i = 0; i < MOTOR_NUM; i++) {
                power_ratio[i] *= speed / max;
            }
        }
    }
    int power[MOTOR_NUM];  // モーターの出力
    for (uint8_t i = 0; i < MOTOR_NUM; i++) {
        power_ratio[i] += pid;                                  // PID制御による出力を加算
        power_ratio[i] = constrain(power_ratio[i], -255, 255);  // 出力を制限
        power[i] = (int)power_ratio[i];                         // 出力を整数に変換して保存
    }
    for (uint8_t i = 0; i < MOTOR_NUM; i++) {
        power[i] = pre_p[i] * POWER_LPF +
                   power[i] * (1 - POWER_LPF);  // 出力にLPFをかける
        pre_p[i] = power[i];                    // 前回の出力を保存
    }
    drive(power);  // モーターを制御
}

// ライン退避
// move_angle: ライン退避する方向
// 機体の角度の補正を行わずに速やかにコート内に退避する
void Motor::esc_line(double move_angle, uint8_t speed) {
    float power_ratio[MOTOR_NUM];  // モーターの出力比
    for (uint8_t i = 0; i < MOTOR_NUM; i++) {
        power_ratio[i] = sin(
            move_angle -
            MOTOR_RAD
                [i]);  // モーターの出力比を計算（計算法については，別途説明）
    }
    double max = 0;  // 最大の出力比
    for (uint8_t i = 0; i < MOTOR_NUM; i++) {
        if (abs(power_ratio[i]) > max) {
            max = abs(power_ratio[i]);
        }
    }
    int power[MOTOR_NUM];  // モーターの出力
    // 出力比が最大のモーターの出力がspeedになるように調整
    if (max > 0) {
        for (uint8_t i = 0; i < MOTOR_NUM; i++) {
            power_ratio[i] *= speed / max;
            power[i] = power_ratio[i];
        }
    }
    drive(power);  // モーターを制御
}

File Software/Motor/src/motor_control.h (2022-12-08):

#include <Arduino.h>

#define MOTOR_NUM 4
#define MAX_PWM 200
#define PWM_FREQ 80000
#define Kp 0.0
#define Ki 0.0
#define Kd 0.0

class Motor {
   public:
    void begin();
    void brake();
    void cal(float go_rad, float gyro_rad, int speed, float machine_rad);
    void move(float *power);

   private:
    const int MOTOR_PIN[MOTOR_NUM][2] = {
        {0, 1}, {2, 3}, {4, 5}, {8, 9}};  // PWM, DIR
    const float MOTOR_POS[MOTOR_NUM] = {0.0, PI / 2.0, PI, 3.0 * PI / 2.0};
    float power[MOTOR_NUM] = {0.0, 0.0, 0.0, 0.0};
};

void Motor::begin() {
    for (int i = 0; i < MOTOR_NUM; i++) {
        pinMode(MOTOR_PIN[i][0], OUTPUT);
        pinMode(MOTOR_PIN[i][1], OUTPUT);
        digitalWrite(MOTOR_PIN[i][0], HIGH);
        pwm(MOTOR_PIN[i][1], PWM_FREQ, 1023.0 / 2.0);
    }
}

void Motor::brake() {
    for (int i = 0; i < MOTOR_NUM; i++) {
        digitalWrite(MOTOR_PIN[i][0], LOW);
        digitalWrite(MOTOR_PIN[i][1], LOW);
    }
}

void Motor::cal(float go_rad, float gyro_rad, int speed, float machine_rad) {
    go_rad = fmod(go_rad, 2.0 * PI);
    gyro_rad = fmod(gyro_rad, 2.0 * PI);
    machine_rad = fmod(machine_rad, 2.0 * PI);
    speed = constrain(speed, -MAX_PWM / 2.0, MAX_PWM / 2.0);
    for (int i = 0; i < MOTOR_NUM; i++) {
        power[i] = sin(go_rad - MOTOR_POS[i]);
    }
    float max_power = 0.0;
    for (int i = 0; i < MOTOR_NUM; i++) {
        if (max_power < abs(power[i])) {
            max_power = abs(power[i]);
        }
    }
    for (int i = 0; i < MOTOR_NUM; i++) {
        power[i] = power[i] / max_power * speed;
    }
    move(power);
}

void Motor::move(float *power) {
    int output[MOTOR_NUM] = {0};
    for (int i = 0; i < MOTOR_NUM; i++) {
        output[i] = (int)(power[i] + 1023.0 / 2.0);
        output[i] = constrain(output[i], 0, MAX_PWM);
    }
    for (int i = 0; i < MOTOR_NUM; i++) {
        digitalWrite(MOTOR_PIN[i][0], HIGH);
        pwm(MOTOR_PIN[i][1], PWM_FREQ, output[i]);
    }
}

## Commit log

2022-08-06 ラインセンサー
2022-08-28 3Dモデル直したよ
    [キッカーマウントハブ.stl, キッカーマウント右.stl, キッカーマウント左.stl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]
2022-08-31 プログラムちょっと書いたよ
    [バックカバー.stl, バッテリーケース.stl, モーターマウントrev2.stl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]
2022-09-01 ラインセンサー書いたよ
2022-09-01 ぷろぐらｍかいた
2022-09-02 ジャイロ
2022-09-04 ジャイロ
    サンプルコードコピペしただけ
    三つとも一応問題なく読める
2022-09-05 ジャイロ(Z軸のみ) 未完成
2022-09-05 Create Motor Mount.stl
    [Motor Mount.stl]
2022-09-06 赤外線 コピー
2022-09-06 ジャイロ まだ誤差が大きい
2022-09-06 ジャイロ 誤差でか
2022-09-07 Create Motor Mount for Pololu.stl
    [Motor Mount for Pololu.stl]
2022-09-08 磁気 修正前
2022-09-08 あいふえｓｈげｒごいうぇｆｋｌぼれｇ
2022-09-08 ジャイロ動いた～
2022-09-11 磁気 角度だせた
2022-09-11 ファイル直した
2022-09-12 ファイル整理
2022-09-12 姿勢制御開始
2022-09-12 Update gyro.cpp
    誤字修正
2022-09-13 姿勢制御ちょっと直してみた
2022-09-13 ジャイロ 姿勢制御 level1
2022-09-13 クラスで書いてみたよ
2022-09-14 姿勢制御
2022-09-15 負の向き 考慮バージョン
2022-09-15 前進＋姿勢制御 成功
2022-09-15 クラス書いた
2022-09-16 うんんちおいしい
2022-09-25 赤外線 クラスにした（つもり）
    未検証
2022-09-26 クラス 赤外線
2022-10-01 ちょっと修正
    [Back Cover.stl, Bottom.stl, Front Left Cover.stl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]
2022-10-08 9軸sennsa
2022-10-09 ラインセンサーとか新しいオムニ計算
    [Top.stl, Universal Mount Hub.stl]
2022-10-10 ジャイロセンサー
2022-10-11 PID姿勢制御（Serial送れない）
2022-10-12 ハードウェア修正
    [Camera Case.stl]
2022-10-12 ジャイロ P制御
2022-10-13 ボール追った
2022-10-14 P制御 ひとまずOK
2022-10-14 ラインセンサ
2022-10-17 赤外線 追えない
2022-10-19 ハードウェア
    [Motor Mount.stl]
2022-10-19 赤外線追う 姿勢制御
    同時はまだ試せてない
2022-10-20 オムニ作ったよ
    [Omni Wheel Main.stl, Omni Wheel Sub.stl]
2022-10-21 ちんちん
    [Omni Wheel Main.stl]
2022-10-21 ライン 逆向き
2022-10-22 ライン 途中
2022-10-25 PID調整
2022-10-25 赤外線垂れ流し
2022-10-28 色々やってみた
2022-10-29 色々いじった
2022-11-01 ライン 圧縮成功確認
2022-11-02 春眠暁を覚えず
2022-11-02 ドストエフスキー
2022-11-02 ラインでけた やったー
2022-11-04 回り込みパーティ プロトタイプ１
    The First Step
2022-11-06 回り込みだぜ
2022-11-06 三号機やで
2022-11-08 参号機 印刷ファイル
    [Back_Cover.stl, Front_Cover.stl, Front_Side_Cover.stl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]
2022-11-08 回り込み 続き
2022-11-08 いつものあれ
2022-11-08 回り込み つづき
    明日
    モーターマウント チェック
    計算なし 値指定
    二輪で横移動
2022-11-09 気にすんな
2022-11-12 色々いっじた
    [Back_Cover.stl, Bottom.stl, Front_Cover.stl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]
2022-11-13 6軸 まだ出せてない
2022-11-13 無かった
2022-11-14 いろじゅｓｇｊせいが
2022-11-14 6軸 角度読めた
2022-11-14 おなじみのごみ
2022-12-05 MPUライブラリ化計画
2022-12-07 mpuをポインターに変える前
2022-12-07 p_mpuを追加
2022-12-07 やっとモーター動いた
    [Handle.stl]
2022-12-08 姿勢制御とオムニ制御
2022-12-08 フォルダ整理した
2022-12-09 ごみ消去
2022-12-09 PIDパラメータいじり はじめました
2022-12-10 インクルードガードの実装、モーターのクラス化
2022-12-11 オムニ制御、姿勢制御、ラインセンサー修正した
2022-12-12 ir直した
2022-12-12 ラインのお準備
2022-12-12 15からD15に変更
2022-12-12 いろいろ
2022-12-13 いろいおｒ
2022-12-13 回り込みユートピア
2022-12-13 ファイル整理とかした
    [ラインセンサ_v1.brd]
2022-12-14 LINE TRACE
2022-12-14 DMP機能実装 ジャイロ完璧
2022-12-15 キャリブレーション
2022-12-15 lineflag導入（不完全）
2022-12-16 お椀関数
2022-12-19 桐生ノード分
2022-12-21 ハードウェア直した
    [Omini_Bottom.stl, Omini_Top.stl]
2022-12-23 回り込みとか
2022-12-27 ライン線sな～と回り込み
2022-12-27 よくわからないけど
2022-12-28 赤外線センサー距離
    [Bottom.stl, Top.stl, ラインセンサ_v1.brd]
2022-12-29 色々やったで
2023-01-02 ちょっと距離算出
2023-01-11 いっｊｔｆ
    [Left Cover.stl, top marker.stl]
2023-01-13 シリアル直した
    [Camera.stl, Front.stl, IR Cover.stl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]
2023-01-16 閾値でつまり侍りき
2023-01-17 conflict 直った（？）
    conflict回避ミスで大変なことになってしまったので、素人目だけれどとりあえずエラー起きそうなところだけ解消したつもり ちゃんと動くかわからない
2023-01-19 ライン計算いろいろ検討中
2023-01-19 ロボット完成間際
2023-01-20 ライン彼岸花
2023-01-21 ラインセンサ周りの改良
2023-01-21 XIAO心だからやめ
2023-01-22 マークダウン
2023-01-22 色々修正した
2023-01-23 line 角度反映できてない
2023-01-24 性凱旋など
    [IR Cover.stl, IR Cover2.stl, Ultra Sonic Holder.stl]
2023-01-24 キーパー
2023-01-25 ロシアバンザイ
    [Ultra Sonic Holder.stl, Ultra Sonic Holder2.stl]
2023-01-27 ▼まわりこめ！
2023-01-28 回り込み＋ライントレース（角以外）
2023-01-28 紆余曲折あったが、結局私はセーブデータにすがることにしたのだ。
2023-01-28 キーパーなど
2023-01-29 試合前のセーブポイント
2023-01-30 大会終わった
2023-02-04 新しく作ったぞい
2023-02-05 名古屋に向けて頑張ろう
2023-03-06 回り込み 中立点解消版
    line_trace_verticalでもライン出ちゃうので
    ・ライン踏んだら常に真逆に進む
    ・ボールが前なら指数円運動
    ・ボールが後ろなら後ろに直進
    中立点ではまらなくなった
2023-03-07 ゴール向け
2023-03-08 モニター
2023-03-16 明日 machine_angle送れてるか試す
2023-03-17 ゴール考慮回り込み
    Goal Weight を角度に応じて変化させたい
2023-03-18 ゴール ガタガタ
2023-03-18 ゴールガタガタ 改善 割と入る
    各角から各中立点への移動を完璧にしたい
2023-03-19 ラインだよ
2023-03-19 キーパー途中
2023-03-19 キーパー ライン セーブポイント
    押されても戻るが
    カーブで脱線する
2023-03-19 ラインそこそこよくなった
2023-03-19 おやすみ。モニターかわいい
2023-03-20 ライン怪しい
2023-03-21 キーパーとアタッカーをそれぞれ調整した。
    [Front.stl, Left Cover.stl, Right Cover.stl]
2023-03-21 メインプログラム疎開完了
    [BLDC_Mount.stl, Back Cover.stl, Back.stl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]
2023-03-22 息もでーーーーーーーーーーーーーーーーーーーーーーーーーーーーーーーーーーーーーーーーーーーーーーーーーーーーーーーーーーーーーーーーーーーーーーーーーーーーーーーーーーーーーーーーーーーーーーーーーーーーーーーーーーーーーーーーーーーーーーーーーーーーーーーーきないくらいの衝撃
2023-04-05 最終更新
2023-04-05 これが最後
2023-05-02 ロボを直したよ
2024-06-11 Hardwareファルダ内のファイルを更新・整理した．
    [Cam Mount.stl, Controller.f3z, MotorDriverMount(DRV8874).f3z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]
2024-06-11 Update README.md
    古くなっていた情報やわかりにくい表現の訂正
2024-06-11 赤外線センサー，モーター制御に関するプログラムを整えた
2024-06-15 コメントを追加
2024-06-15 FWのライン処理にコメントを追加
2024-06-15 Pico Main GKにもコメントを追加した(途中)
